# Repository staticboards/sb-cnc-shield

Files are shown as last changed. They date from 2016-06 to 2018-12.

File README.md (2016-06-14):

# This is the staticboards Arduino CNC shield for low-cost CNC machines.

This is a rework of the original arduino cnc shiled http://blog.protoneer.co.nz/arduino-cnc-shield/

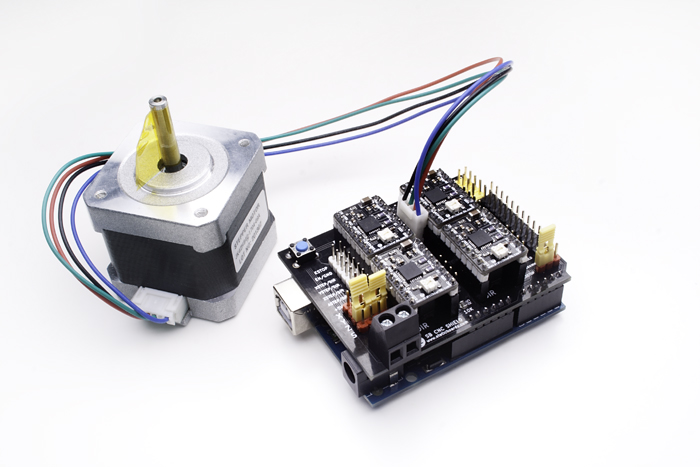
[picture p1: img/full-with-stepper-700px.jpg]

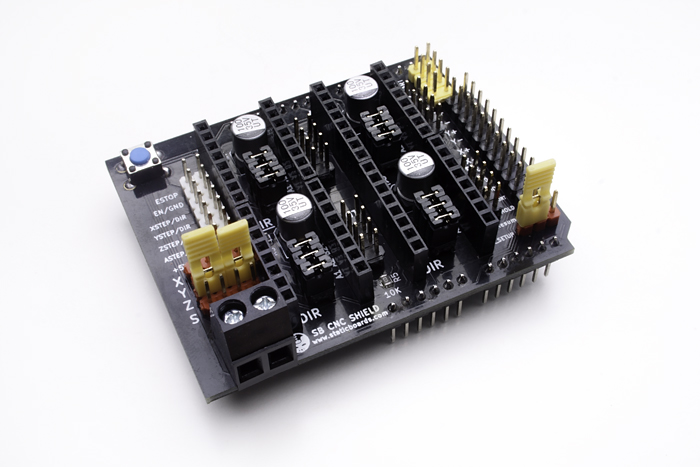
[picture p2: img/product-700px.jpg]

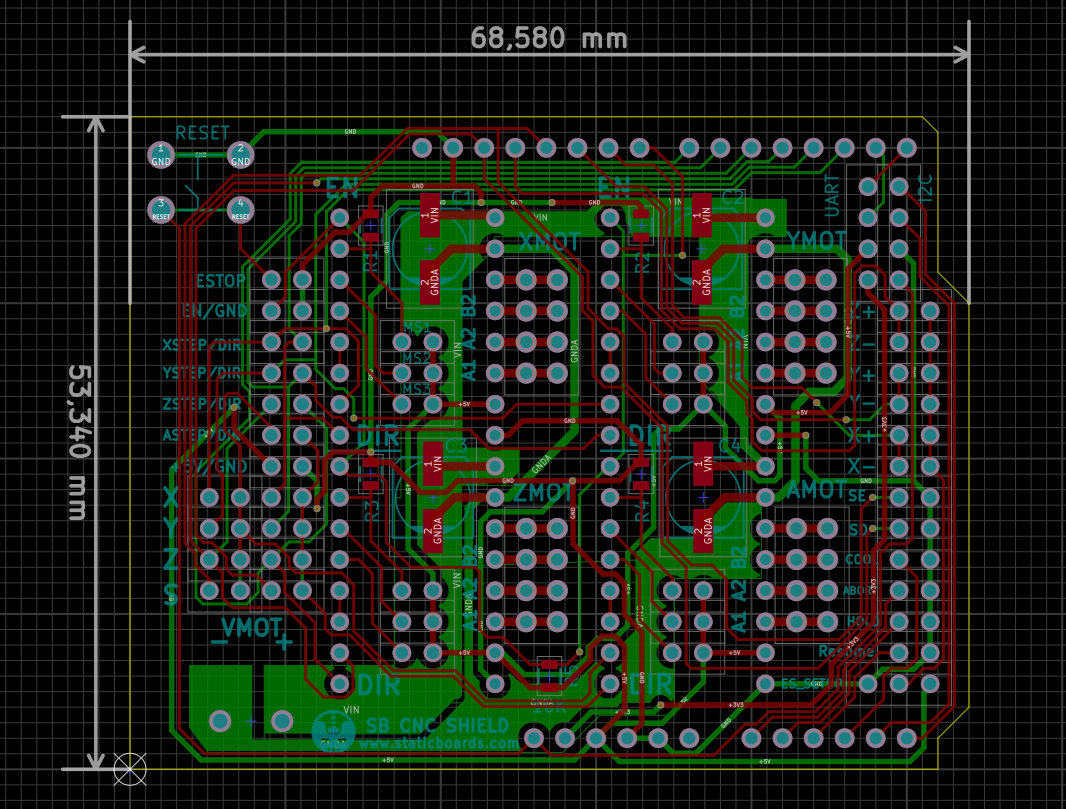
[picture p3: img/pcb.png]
staticboards Arduino CNC shield PCB

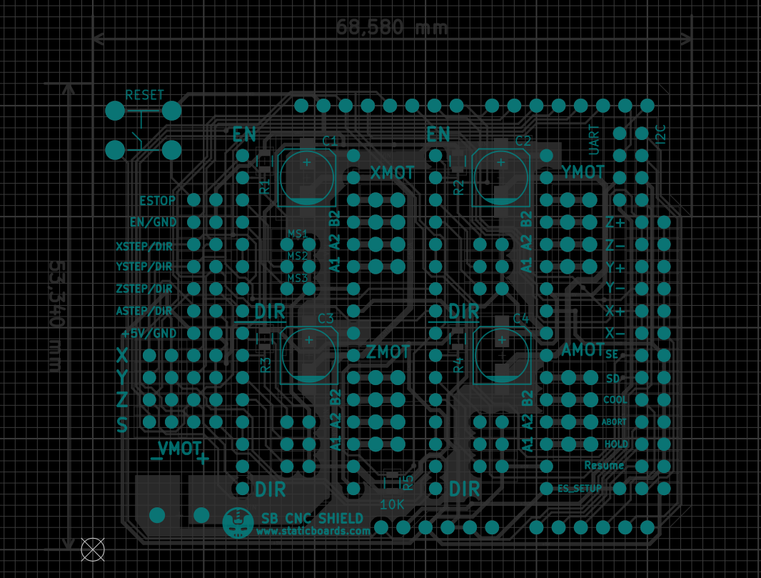
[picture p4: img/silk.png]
staticboards Arduino CNC shield Silk Screen

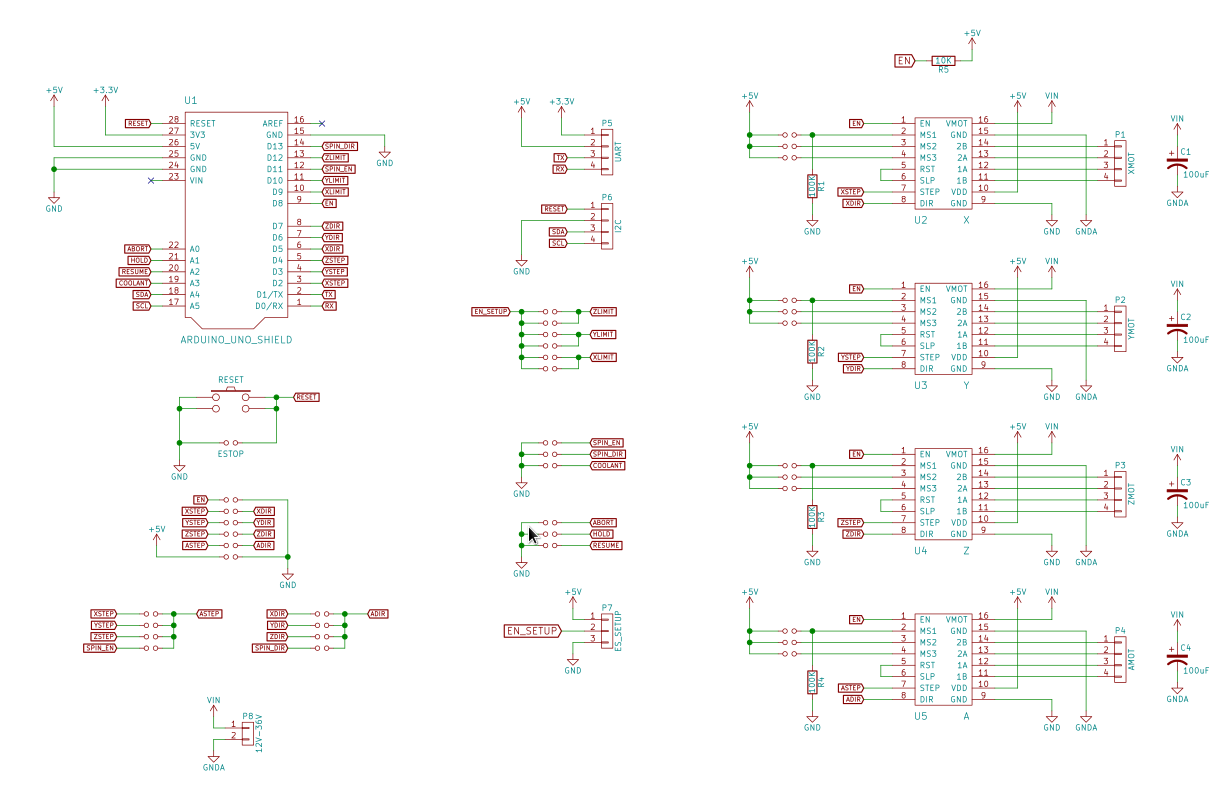
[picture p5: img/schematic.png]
staticboards Arduino CNC shield Schematic


## Why did you make a new Arduino CNC shield?

We were trying to make a new **low-cost** CNC machine for makers and hobbyist.

We found that it is not hard to design a simple aluminum structure with some 3d printed parts, using open software like FreeCAD.

But surprising, there are not many options for electronics part. And we didn’t find any open source shield for Arduino. Maybe we are wrong! But with a quick search, we didn't find anything.

We found one **Arduino CNC** shield that is being sold on eBay or Aliexpress. But the authors don’t like the idea of Chinese manufacturers making boards without any real collaboration (*something that I agree, open hardware is about community*). I couldnt find source files for this board.

So, as we decided that it is time to learn KiCad (a real open source software for PCB design), and we decided to make the PCB of this board, using the same pin layout, to get experience with KiCad.

And this is the final result: The **SB CNC Shield for Arduino Uno, 100% compatible with GRBL**.

We followed the same philosophy of our popular RAMPS 1.4 SB: Branded components, like the Molex connector, beautiful design with the black PCB and golden finish, and fully tested before shipping.

## What can you do with the SB CNC Shield?

The main idea behind this shield is that you can make your own functional CNC with a limited budget.

If you are interested in robots, you should make your own CNC machine. There are many problems that are not obvious at first. Motors, drivers, heat, software, belts, backslash.

Even if you want to buy an expensive machine, and you don't have any previous experience with CNC, it is a very good idea to make one by yourself.

**SB CNC SHIELD is 100% open hardware**. It is designed with *KiCad*, and you can read the schematics, check the PCB design, learn about electronics, improve it, whatever.

And the most important part with Open Hardware, we can create a community, share experiences, new ideas and fix problems.

This board is 100% compatible with the popular GRBL firmware. You don't need special configurations. Plug and Play. 

And there is a huge community behind this project, You can be part of it!

## Why no a full CNC board?

Well, you can go with a complete board. If you are serious about CNC, you should do it. A complete board is autonomous. You don't need a computer to send commands to the machine.

There are some boards open source, with a good community. That is very important if you want good support.
But most of them, they are closed source. Or they have a custom firmware.

For example, some integrated boards include the drivers within the board. That could be a problem. Drivers can get hot and it is not difficult to burn one. And in some cases, it is a good idea to use different drivers for each axis. 

And they have a higher price. Usually more than $100. If you are making a small CNC, for casual projects, this is a big deal.

## What else do I need?

To build a complete CNC machine you will need:

- One Arduino Uno
- At least, 3 drivers for the motors (you can use the popular A4988, or the more powerful DRV8825)
- One bipolar stepper motor for each axis
- One power supply. You can reuse your PC power supply with our ATX Board.
- The spindle (you can use a Dremel or buy a spindle on eBay) or a laser diode.
- The structure (aluminum t-slots, printed parts, etc)

## SB CNC Shield Features

- Beautiful design in Black. With Gold finish,  colored pin headers and a blue reset button.
- Cute easy yellow jumpers!
- 100% Compatible with the GRBL firmware. Plug and Play.
- You can duplicate any axis, or sacrifice your spindle control for a 4th axis. Simply change the jumpers, and duplicate any axis.
- Molex power connector rated at 15A. Cheap Chinese plastic connectors can get burned.
- You can use AWG22 cables for the power supply.
- 35V Capacitors. You can use 24V power supplies without any problem.-
- Endstops for X,Y,Z. You can connect the maximum and minimum limit for each axis.
- Easy to Access Reset button
- Configurable Emergency Button (normally open or normally closed)
- You can use the PWM features in GRBL to control the spindle speed. This is a great feature for metal and wood works.
- You can configure micro stepping for each driver, for a fluid movement.
- External driver connector. You can use professional and expensive drivers, like the Gecko drivers.
- You can use the extended pins from GRBL, like Coolant, Pause/Hold, Resume, and Abort
- UART connectors. You can use a Bluetooth adapter for a wireless CNC machine.
- i2c connection. You can use a temperature sensor for example (but you have to modify the GRBL source code)

## Useful Links

- http://blog.protoneer.co.nz/arduino-cnc-shield/ Original design. It has many guides and tutorials.
- https://github.com/grbl/grbl : GRBL firmware. You should learn how to use it
- https://github.com/winder/Universal-G-Code-Sender Graphical Interface, written in Java
- https://www.staticboards.com/ : Our website
- https://github.com/staticboards/sb-cnc-shield : github original repository

## License

**Creative-Commons 3.0 CC BY-SA**

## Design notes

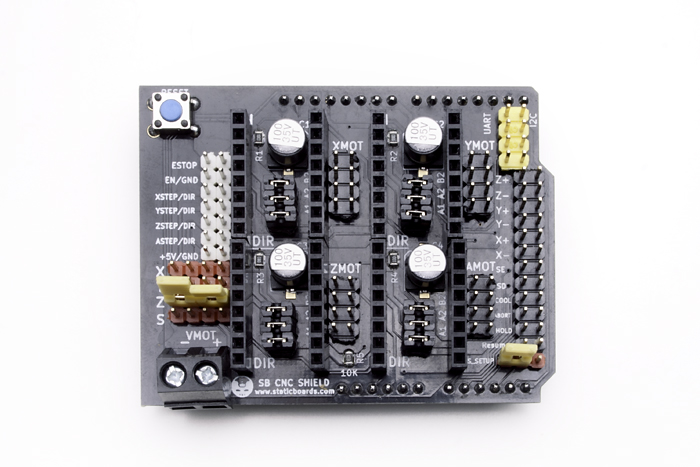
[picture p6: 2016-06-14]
img/top-700px.jpg

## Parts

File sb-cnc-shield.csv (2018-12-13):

Reference | Value | Footprint | Datasheet
U1 | ARDUINO_UNO_SHIELD | footprints:ARDUINO_SHIELD
U5 | A | footprints:POLOLU_STEPPER_DRIVER
U3 | Y | footprints:POLOLU_STEPPER_DRIVER
U2 | X | footprints:POLOLU_STEPPER_DRIVER
U4 | Z | footprints:POLOLU_STEPPER_DRIVER
P1 | XMOT | Pin_Headers:Pin_Header_Straight_2x04
P2 | YMOT | Pin_Headers:Pin_Header_Straight_2x04
P3 | ZMOT | Pin_Headers:Pin_Header_Straight_2x04
P4 | AMOT | Pin_Headers:Pin_Header_Straight_2x04
JP1 | Jumper_NO_Small | footprints:Pin_100mil_Header_Straight_1x02
JP2 | Jumper_NO_Small | footprints:Pin_100mil_Header_Straight_1x02
JP3 | Jumper_NO_Small | footprints:Pin_100mil_Header_Straight_1x02
R1 | 100K | Resistors_SMD:R_0805
R2 | 100K | Resistors_SMD:R_0805
JP4 | Jumper_NO_Small | footprints:Pin_100mil_Header_Straight_1x02
JP5 | Jumper_NO_Small | footprints:Pin_100mil_Header_Straight_1x02
JP6 | Jumper_NO_Small | footprints:Pin_100mil_Header_Straight_1x02
JP7 | Jumper_NO_Small | footprints:Pin_100mil_Header_Straight_1x02
JP8 | Jumper_NO_Small | footprints:Pin_100mil_Header_Straight_1x02
JP9 | Jumper_NO_Small | footprints:Pin_100mil_Header_Straight_1x02
R3 | 100K | Resistors_SMD:R_0805
JP10 | Jumper_NO_Small | footprints:Pin_100mil_Header_Straight_1x02
JP11 | Jumper_NO_Small | footprints:Pin_100mil_Header_Straight_1x02
JP12 | Jumper_NO_Small | footprints:Pin_100mil_Header_Straight_1x02
R4 | 100K | Resistors_SMD:R_0805
C1 | 100uF | Capacitors_SMD:c_elec_6.3x7.7
C2 | 100uF | Capacitors_SMD:c_elec_6.3x7.7
C3 | 100uF | Capacitors_SMD:c_elec_6.3x7.7
C4 | 100uF | Capacitors_SMD:c_elec_6.3x7.7
P5 | UART | Pin_Headers:Pin_Header_Straight_1x04
P6 | I2C | Pin_Headers:Pin_Header_Straight_1x04
JP13 | Z+ | footprints:Pin_100mil_Header_Straight_1x02
JP14 | Z- | footprints:Pin_100mil_Header_Straight_1x02
JP15 | Y+ | footprints:Pin_100mil_Header_Straight_1x02
JP16 | Y- | footprints:Pin_100mil_Header_Straight_1x02
JP17 | X+ | footprints:Pin_100mil_Header_Straight_1x02
JP18 | X- | footprints:Pin_100mil_Header_Straight_1x02
JP19 | SpinEn | footprints:Pin_100mil_Header_Straight_1x02
JP20 | SpinDir | footprints:Pin_100mil_Header_Straight_1x02
JP21 | CoolEn | footprints:Pin_100mil_Header_Straight_1x02
JP22 | Abort | footprints:Pin_100mil_Header_Straight_1x02
JP23 | Hold | footprints:Pin_100mil_Header_Straight_1x02
JP24 | Resume | footprints:Pin_100mil_Header_Straight_1x02
P7 | ES_SETUP | Pin_Headers:Pin_Header_Straight_1x03
SW1 | RESET | footprints:SWITCH_TACTILE_6.5_PTH
JP25 | ESTOP | footprints:Pin_100mil_Header_Straight_1x02
JP26 | EN/GND | footprints:Pin_100mil_Header_Straight_1x02
JP27 | XSTEP/DIR | footprints:Pin_100mil_Header_Straight_1x02
JP28 | YSTEP/DIR | footprints:Pin_100mil_Header_Straight_1x02
JP29 | ZSTEP/DIR | footprints:Pin_100mil_Header_Straight_1x02
JP30 | ASTEP/DIR | footprints:Pin_100mil_Header_Straight_1x02
JP31 | +5V/GND | footprints:Pin_100mil_Header_Straight_1x02
JP32 | Jumper_NO_Small | footprints:Pin_100mil_Header_Straight_1x02
JP33 | Jumper_NO_Small | footprints:Pin_100mil_Header_Straight_1x02
JP34 | Jumper_NO_Small | footprints:Pin_100mil_Header_Straight_1x02
JP35 | Jumper_NO_Small | footprints:Pin_100mil_Header_Straight_1x02
JP36 | Jumper_NO_Small | footprints:Pin_100mil_Header_Straight_1x02
JP37 | Jumper_NO_Small | footprints:Pin_100mil_Header_Straight_1x02
JP38 | Jumper_NO_Small | footprints:Pin_100mil_Header_Straight_1x02
JP39 | Jumper_NO_Small | footprints:Pin_100mil_Header_Straight_1x02
P8 | 12V-36V | footprints:CONN_01x02_PITCH_5.08mm
R5 | 10K | Resistors_SMD:R_0805

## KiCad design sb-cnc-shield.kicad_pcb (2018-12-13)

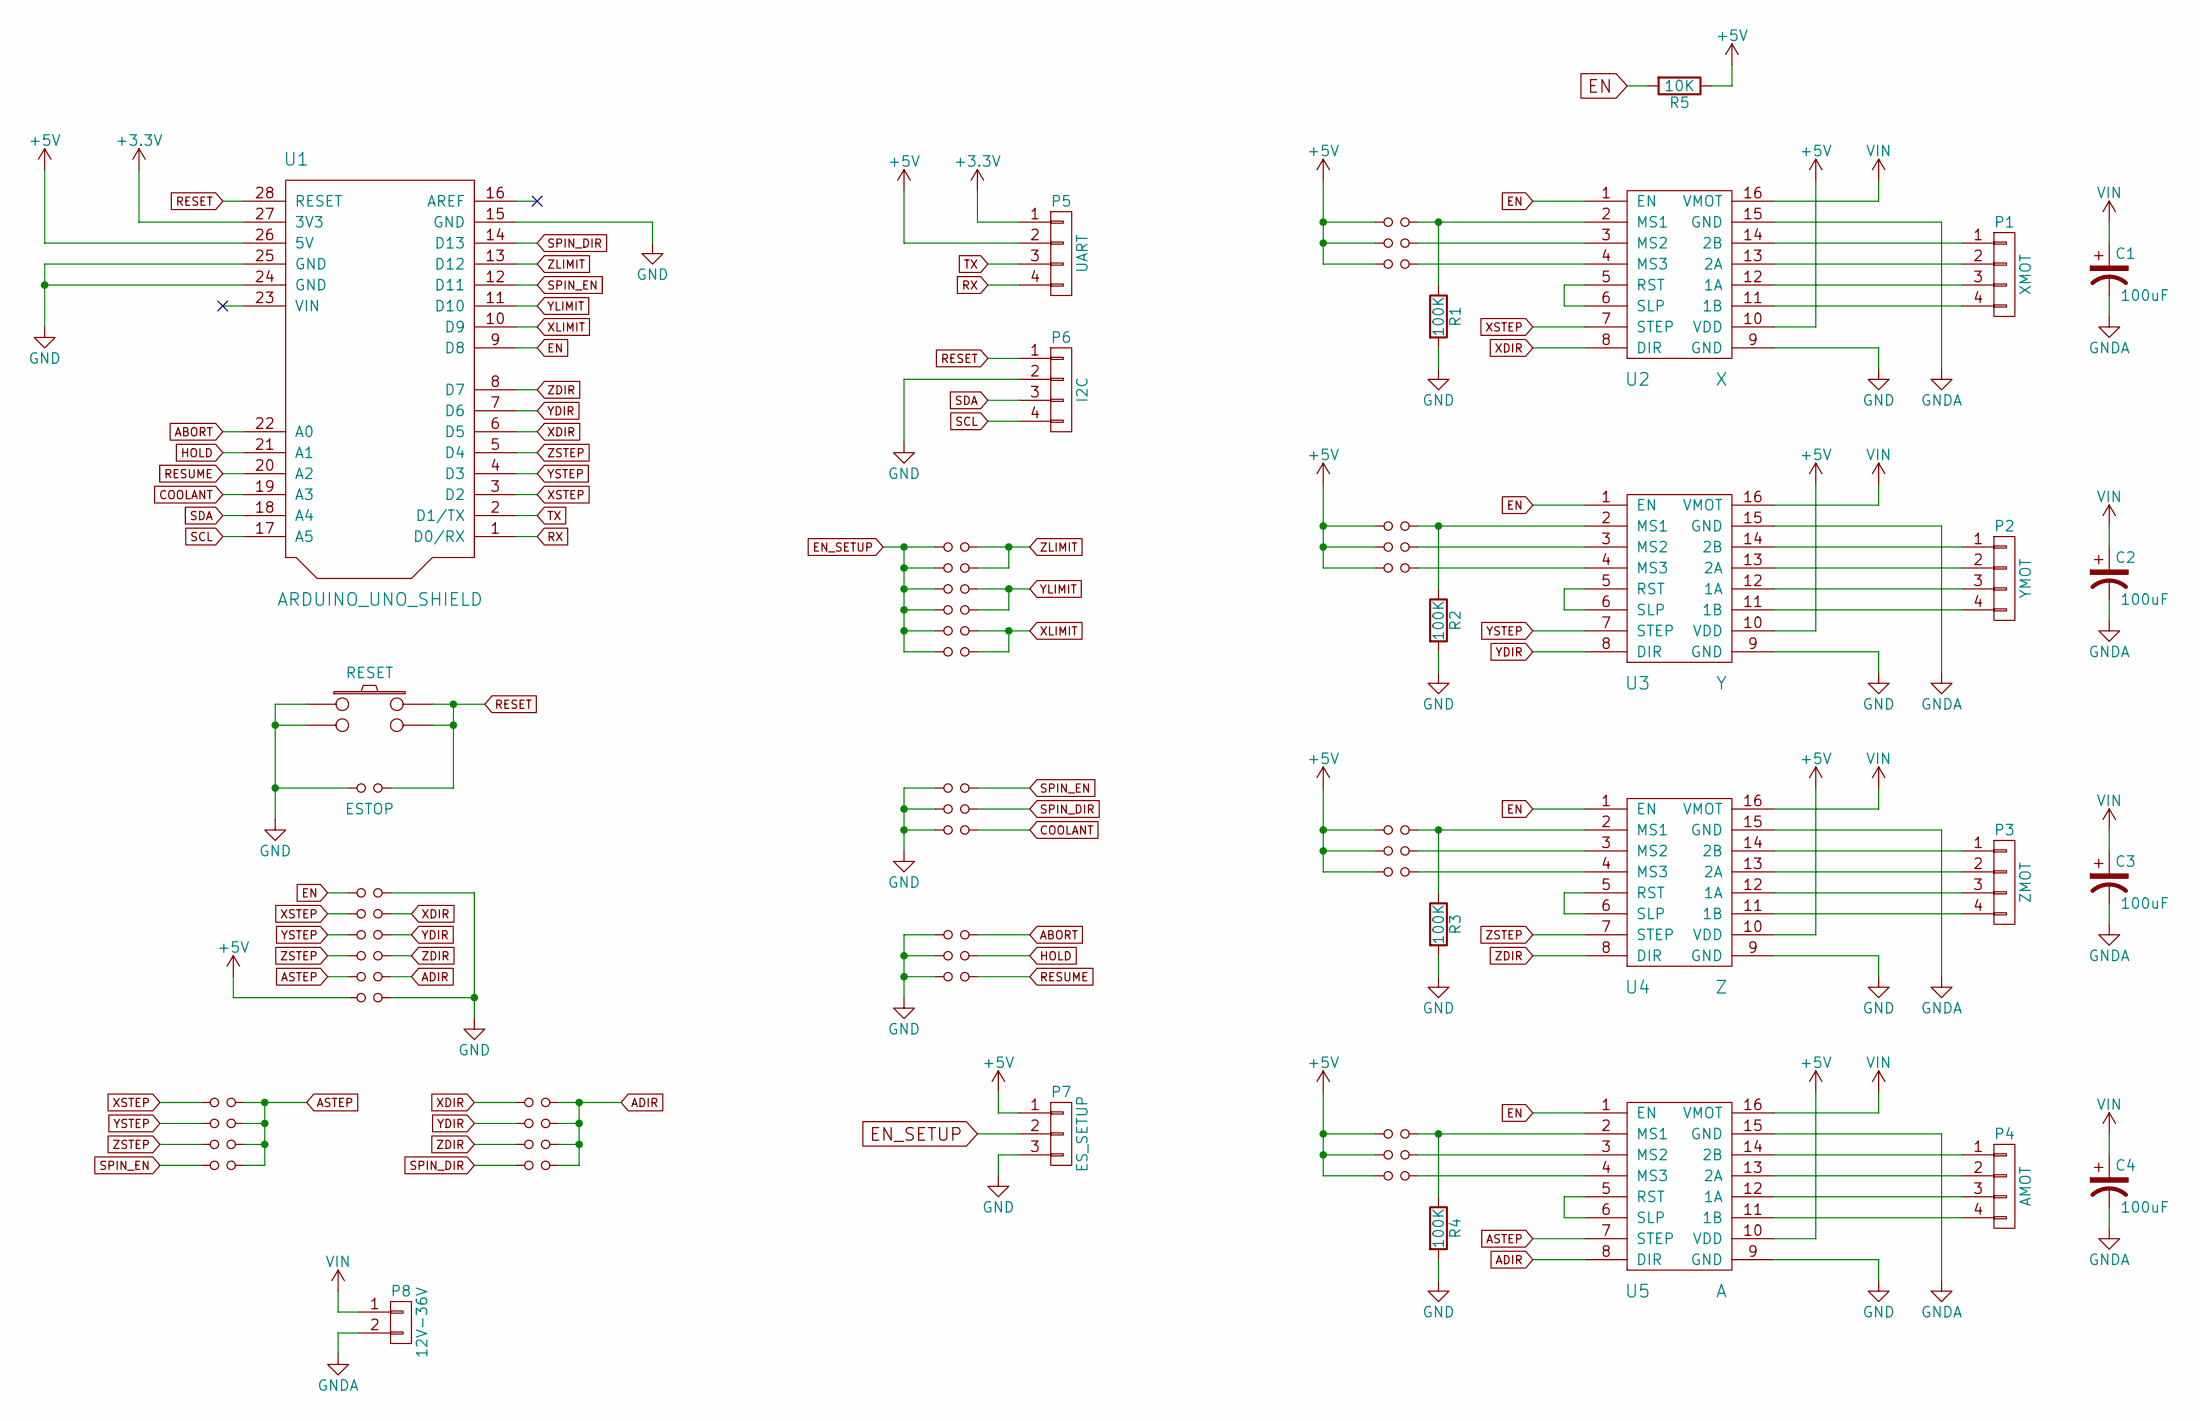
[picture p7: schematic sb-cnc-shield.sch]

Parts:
C1, C2, C3, C4: 100uF; c_elec_6.3x7.7
JP1, JP2, JP3, JP4, JP5, JP6, JP7, JP8, JP9, JP10, JP11, JP12, JP32, JP33, JP34, JP35, JP36, JP37, JP38, JP39: Jumper_NO_Small; Pin_100mil_Header_Straight_1x02
JP13: Z+; Pin_100mil_Header_Straight_1x02
JP14: Z-; Pin_100mil_Header_Straight_1x02
JP15: Y+; Pin_100mil_Header_Straight_1x02
JP16: Y-; Pin_100mil_Header_Straight_1x02
JP17: X+; Pin_100mil_Header_Straight_1x02
JP18: X-; Pin_100mil_Header_Straight_1x02
JP19: SpinEn; Pin_100mil_Header_Straight_1x02
JP20: SpinDir; Pin_100mil_Header_Straight_1x02
JP21: CoolEn; Pin_100mil_Header_Straight_1x02
JP22: Abort; Pin_100mil_Header_Straight_1x02
JP23: Hold; Pin_100mil_Header_Straight_1x02
JP24: Resume; Pin_100mil_Header_Straight_1x02
JP25: ESTOP; Pin_100mil_Header_Straight_1x02
JP26: EN/GND; Pin_100mil_Header_Straight_1x02
JP27: XSTEP/DIR; Pin_100mil_Header_Straight_1x02
JP28: YSTEP/DIR; Pin_100mil_Header_Straight_1x02
JP29: ZSTEP/DIR; Pin_100mil_Header_Straight_1x02
JP30: ASTEP/DIR; Pin_100mil_Header_Straight_1x02
JP31: +5V/GND; Pin_100mil_Header_Straight_1x02
P1: XMOT; Pin_Header_Straight_2x04
P2: YMOT; Pin_Header_Straight_2x04
P3: ZMOT; Pin_Header_Straight_2x04
P4: AMOT; Pin_Header_Straight_2x04
P5: UART; Pin_Header_Straight_1x04
P6: I2C; Pin_Header_Straight_1x04
P7: ES_SETUP; Pin_Header_Straight_1x03
P8: 12V-36V; CONN_01x02_PITCH_5.08mm
R1, R2, R3, R4: 100K; R_0805
R5: 10K; R_0805
SW1: RESET; SWITCH_TACTILE_6.5_PTH
U1: ARDUINO_UNO_SHIELD; ARDUINO_SHIELD
U2: X; POLOLU_STEPPER_DRIVER
U3: Y; POLOLU_STEPPER_DRIVER
U4: Z; POLOLU_STEPPER_DRIVER
U5: A; POLOLU_STEPPER_DRIVER

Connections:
+3V3: P5.1, U1.27 (3V3)
+5V: JP1.1, JP2.1, JP3.1, JP4.1, JP5.1, JP6.1, JP7.1, JP8.1, JP9.1, JP10.1, JP11.1, JP12.1, JP31.1, P5.2, P7.1, R5.1, U1.26 (5V), U2.10 (VDD), U3.10 (VDD), U4.10 (VDD), U5.10 (VDD)
ABORT: JP22.2, U1.22 (A0)
ADIR: JP30.2, JP36.2, JP37.2, JP38.2, JP39.2, U5.8 (DIR)
ASTEP: JP30.1, JP32.2, JP33.2, JP34.2, JP35.2, U5.7 (STEP)
COOLANT: JP21.2, U1.19 (A3)
EN: JP26.1, R5.2, U1.9 (D8), U2.1 (EN), U3.1 (EN), U4.1 (EN), U5.1 (EN)
EN_SETUP: JP13.1, JP14.1, JP15.1, JP16.1, JP17.1, JP18.1, P7.2
GND: JP19.1, JP20.1, JP21.1, JP22.1, JP23.1, JP24.1, JP25.1, JP26.2, JP31.2, P6.2, P7.3, R1.2, R2.2, R3.2, R4.2, SW1.1, SW1.2, U1.15 (GND), U1.24 (GND), U1.25 (GND), U2.9 (GND), U3.9 (GND), U4.9 (GND), U5.9 (GND)
GNDA: C1.2, C2.2, C3.2, C4.2, P8.2, U2.15 (GND), U3.15 (GND), U4.15 (GND), U5.15 (GND)
HOLD: JP23.2, U1.21 (A1)
unnamed: JP1.2, R1.1, U2.2 (MS1)
unnamed: JP2.2, U2.3 (MS2)
unnamed: JP3.2, U2.4 (MS3)
unnamed: JP4.2, R2.1, U3.2 (MS1)
unnamed: JP5.2, U3.3 (MS2)
unnamed: JP6.2, U3.4 (MS3)
unnamed: JP7.2, R3.1, U4.2 (MS1)
unnamed: JP8.2, U4.3 (MS2)
unnamed: JP9.2, U4.4 (MS3)
unnamed: JP10.2, R4.1, U5.2 (MS1)
unnamed: JP11.2, U5.3 (MS2)
unnamed: JP12.2, U5.4 (MS3)
unnamed: P1.1, U2.14 (2B)
unnamed: P1.2, U2.13 (2A)
unnamed: P1.3, U2.12 (1A)
unnamed: P1.4, U2.11 (1B)
unnamed: P2.1, U3.14 (2B)
unnamed: P2.2, U3.13 (2A)
unnamed: P2.3, U3.12 (1A)
unnamed: P2.4, U3.11 (1B)
unnamed: P3.1, U4.14 (2B)
unnamed: P3.2, U4.13 (2A)
unnamed: P3.3, U4.12 (1A)
unnamed: P3.4, U4.11 (1B)
unnamed: P4.1, U5.14 (2B)
unnamed: P4.2, U5.13 (2A)
unnamed: P4.3, U5.12 (1A)
unnamed: P4.4, U5.11 (1B)
unnamed: U2.5 (RST), U2.6 (SLP)
unnamed: U3.5 (RST), U3.6 (SLP)
unnamed: U4.5 (RST), U4.6 (SLP)
unnamed: U5.5 (RST), U5.6 (SLP)
RESET: JP25.2, P6.1, SW1.3, SW1.4, U1.28 (RESET)
RESUME: JP24.2, U1.20 (A2)
RX: P5.4, U1.1 (D0/RX)
SCL: P6.4, U1.17 (A5)
SDA: P6.3, U1.18 (A4)
SPIN_DIR: JP20.2, JP39.1, U1.14 (D13)
SPIN_EN: JP19.2, JP35.1, U1.12 (D11)
TX: P5.3, U1.2 (D1/TX)
VIN: C1.1, C2.1, C3.1, C4.1, P8.1, U2.16 (VMOT), U3.16 (VMOT), U4.16 (VMOT), U5.16 (VMOT)
XDIR: JP27.2, JP36.1, U1.6 (D5), U2.8 (DIR)
XLIMIT: JP17.2, JP18.2, U1.10 (D9)
XSTEP: JP27.1, JP32.1, U1.3 (D2), U2.7 (STEP)
YDIR: JP28.2, JP37.1, U1.7 (D6), U3.8 (DIR)
YLIMIT: JP15.2, JP16.2, U1.11 (D10)
YSTEP: JP28.1, JP33.1, U1.4 (D3), U3.7 (STEP)
ZDIR: JP29.2, JP38.1, U1.8 (D7), U4.8 (DIR)
ZLIMIT: JP13.2, JP14.2, U1.13 (D12)
ZSTEP: JP29.1, JP34.1, U1.5 (D4), U4.7 (STEP)

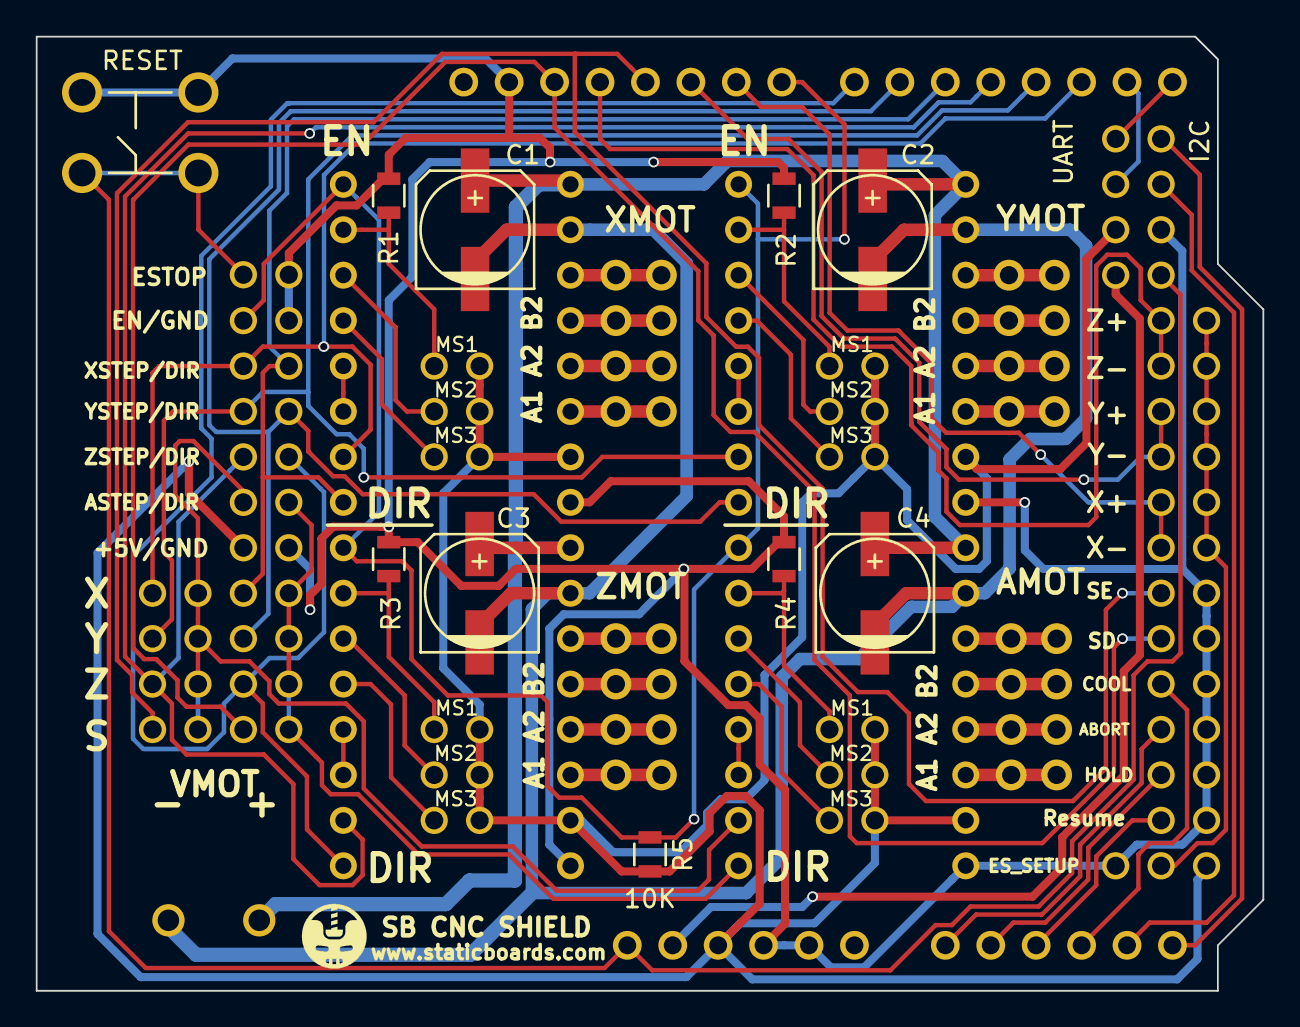
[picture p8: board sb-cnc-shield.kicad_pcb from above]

Board: 2 copper layers, 68.6 x 53.3 mm, 62 parts (0 on the bottom side), 61 nets.

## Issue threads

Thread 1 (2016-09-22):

New versions

cmsteinBR, 2016-09-22:
Dear,
First, congratulations for the job.
This board is based on protoneer cnc shield v3, right?
The latest version is 3.51.
v3.51:
- noise filters on the end-stops;
- probe pins.

There is another similar board: GRBL breakout shield (http://3dtek.xyz/pages/2).
GRBL breakout:
- filter capacitors for the end-stops;
- fan connector and voltage selector;
- holes for a 20 or 40mm fan;
- probe pin.

There are plans to include some of these changes on the board?

Thanks

Closed 2016-10-05.

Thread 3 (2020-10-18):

No class to free programing with the board

kirk-loeten, 2020-10-18:
Are you interested in a class to programing this board? I didn't found one. I found much use cases with GRBL. I could do this in a few weeks.

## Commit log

2016-06-08 sb cnc shield
    [sb-cnc-shield.kicad_pcb, sb-cnc-shield.sch]
2018-12-13 upgraded to kicad 5
    [sb-cnc-shield.csv, sb-cnc-shield.kicad_pcb, sb-cnc-shield.sch]
